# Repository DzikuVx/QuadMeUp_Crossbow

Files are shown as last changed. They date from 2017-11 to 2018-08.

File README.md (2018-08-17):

# QuadMeUp Crossbow

_QuadMeUp Crossbow_ is a DIY project that gives 5km (at least) of RC link for UAV (airplanes and drones) for a price below $40. I uses SX1278 (LoRa 868MHz/915MHz) compatible (like HopeRF RFM95W) radio modules connected to Arduino compatible boards. It can be regular Arduino connected via SPI to SX1278 or dedicated board like _Adafruit Feather 32u4 RFM LoRa_ or [LoRa32u4 II](http://bit.ly/2nJv9dd)

Future versions might be ported to [ESP32 LoRa32 modules](http://bit.ly/2BjG47d).

# Current state

Works:
* Getting data from OpenTX radio using SBUS protocol
* Transmitting 10 channels to RX modules
* Frequency hopping
* Getting basic telemetry from RX module
* Sending 10 channels using SBUS to flight controller
* Binding
* Allowing to use OLED on TX to get basic data

Needs implementation:
* TX module configuration
* RX configuration from TX module
* Sending telemetry from TX to OpenTX radio

# Dependencies

To compile, following libraries have to be installed:

* [U8g2](https://github.com/olikraus/u8g2) for OLED support in TX module
* [FlashStorage](https://github.com/cmaglie/FlashStorage) for EEPROM-Emulation if using a SAMD-Board (M0 etc.)

# Protocol

| Byte | Description | Notes |
| ---- | ---- | ---- |
| 1 | Frame type & used radio channel | bits 7-5 defines frame, bits 4-0 current radio channel |
| 2 - 33 | Payload | lenghth defined by frame type |
| payload length + 2 | CRC | using crc8_dvb_s2 method |

## CRC

CRC is computed using `crc8_dvb_s2` method. Initial CRC value for each frame CRC is equal to CRC of 4 bind bytes (unique for transmitter module). 

## Frame types

| Value  | Value hex | Description | Direction  | Payload length |
| ---- | ---- |---- | ---- | ---- |
| 0000 | 0x0 | RC channels data `RC_DATA` | TX -> RX | 9 |
| 0001 | 0x1 | Receiver health and basic telemetry `RX_HEALTH` | RX -> TX | 6 |
| 0010 | 0x2 | Request receiver configuration | TX -> RX | no used |
| 0011 | 0x3 | Receiver configuration | RX -> TX | no used |
| 0100 | 0x4 | Set receiver configuration | TX -> RX | no used |
| 0101 | 0x5 | PING frame, uses 9 byte payload | TX -> RX | 4 |
| 0110 | 0x6 | PONG frame, the same payload as PING | RX -> TX | 4 |
| 0111 | 0x7 | `BIND` frame, transmitted by TX only during binding | TX -> RX | 4 |

### `RC_DATA` frame format

Protocol allows to send 10 RC channels in total encoded as following

* channels 1 to 4 encoded using 10 bits each (5 bytes)
* channels 5 to 6 encoded using 8 bits each (2 bytes)
* channels 7 to 10 encoded using 4 bits per channel (2 bytes)

Total length of `RC_DATA` payload is 9 bytes

### `RX_HEALTH` frame format

| Byte  | Description |
| ----  | ---- |
| 1 | RX RSSI |
| 2 | RX SNR | 
| 3 | RX supply volatage, sent in 0,1V |
| 4 | RX analog input 1 sent in 0,1V |
| 5 | RX analog input 2 sent in 0,1V |
| 6 | Flags |

#### Flags

| Bit | Meaning |
| ----  | ---- |
| 00000001  | Device in Failsafe mode |

### `PING` and `PONG` frames

`PING` and `PONG` frames are to determine packet roundrip between **TX** and **RX** module.
**TX** sends `PING` frame with curent `micros`. If **RX** receives `PING` frame, it respons
its payload as `PONG` frame. 

### `BIND` frame format

| Byte  | Description |
| ----  | ---- |
| 1 | Bind key byte 0 |
| 2 | Bind key byte 1 |
| 3 | Bind key byte 2 |
| 4 | Bind key byte 3 |

# RSSI

1. Receiver RSSI for the last received packet is injected as channel 11
1. RSSI is scaled in **dB**, NOT **percent**
1. RSSI 0 in flight controller means 40dB RSSI in RF chip on last packet received  
1. RSSI 100 in flight controller means 140dB RSSI in RF chip on last packet received
1. Rule of thumb: to increase distance twice you need 6dB assuming nothing else will interfere
1. If at 100m RSSI is 40, at 200m should be around 34
1. I had successful flight with RSSI below `15`
1. With correct antennas, at 1km RSSI should be around `20` 

# OpenTX setup

OpenTX 2.2.1 or newer is required with enabled **External RF** SBUS.

* Mode: `SBUS`
* Channel Range: `1-16`
* Refresh rate: `12.0ms` or `14.0ms` `normal`

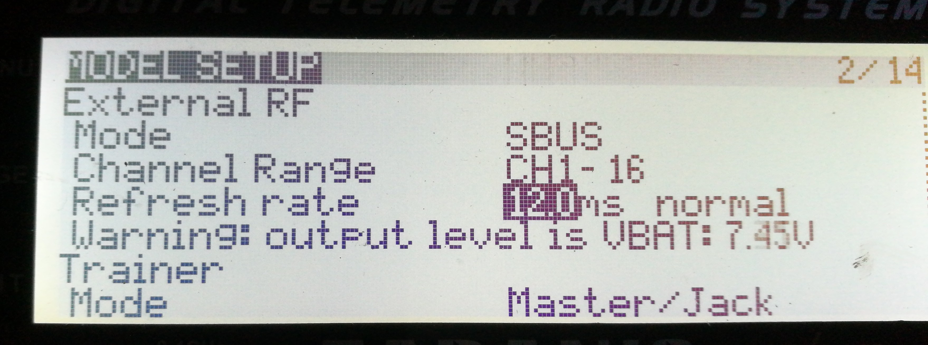
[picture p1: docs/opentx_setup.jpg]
OpenTX setup


Tested with:

* FrSky X9D Plus

# Flight controller setup

RX module outputs RC data using SBUS protocol. The trick is that DIY RX module does not have inverters, so SBUS signal is also not inverted (TTL standard), while standard SBUS protocol used inverted serial signal.

That mean the following:

* RX module TX line can be connected to any free UART RX pin
* On F3 or F7 boards flight controller has to be configured not to use inverted SBUS (refer to flight controller docs)
* On F4 flight controllers inverios has to be configured only when using dedicated SBUS serial port 

# Manual

## Binding

After flashing TX and RX, binding is required. 

1. Power up TX module
1. Navigate using button #1 to "Bind" option
1. Long press button #2 to enter _Bind Mode_
1. Power up RX
1. RX LED flashes quickly when in bind mode
1. After RX receives bind packet, LED goes to constanly _ON_ state
1. When RX LED is solid _ON_, leave bind mode by long pressing button #2 

# TX module connection diagram

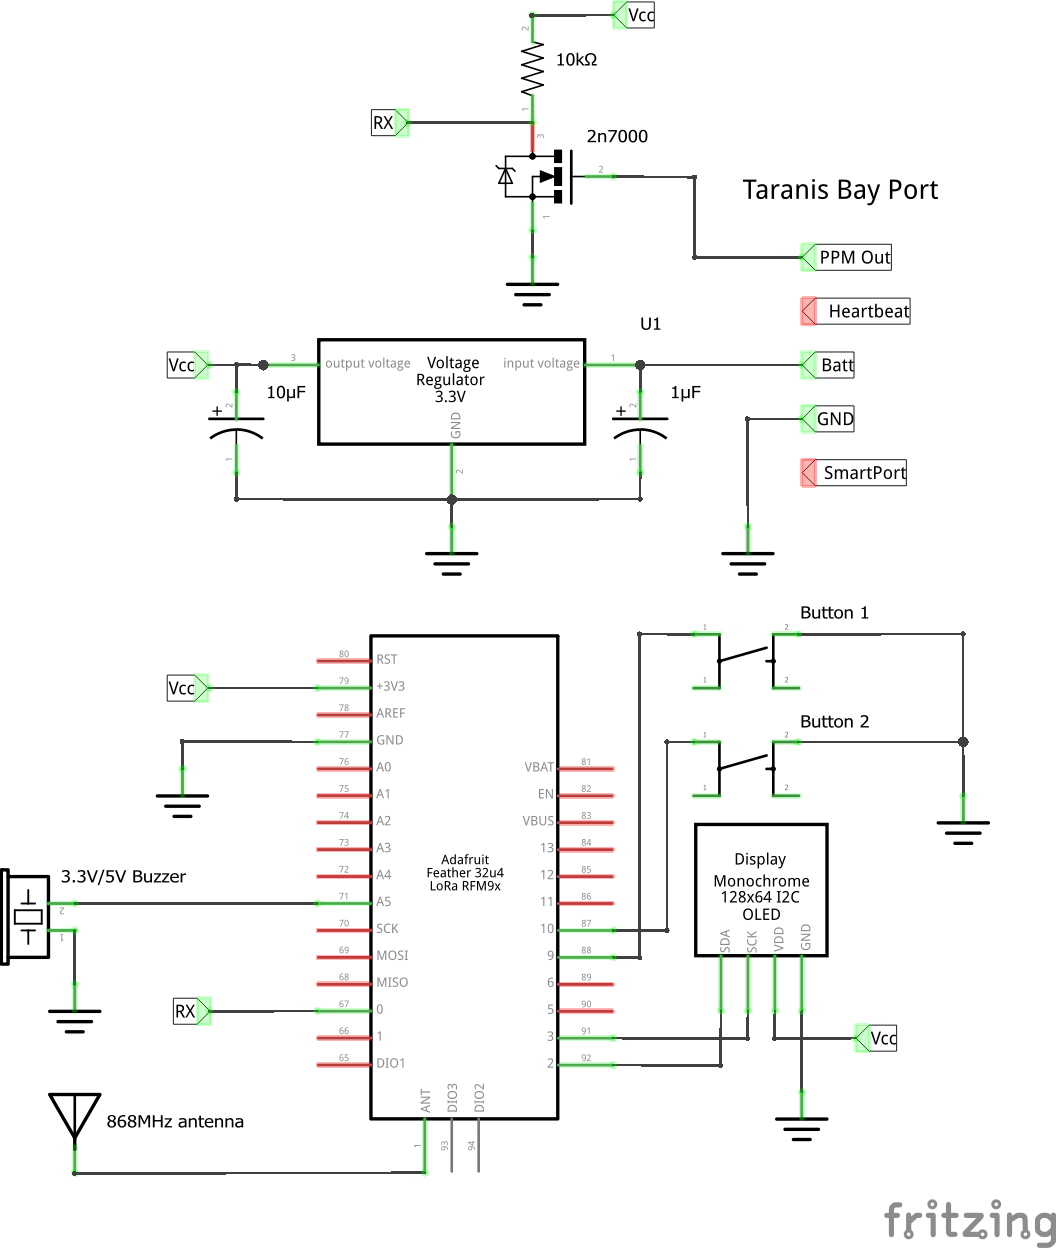
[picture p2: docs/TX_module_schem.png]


# RX module connection diagram

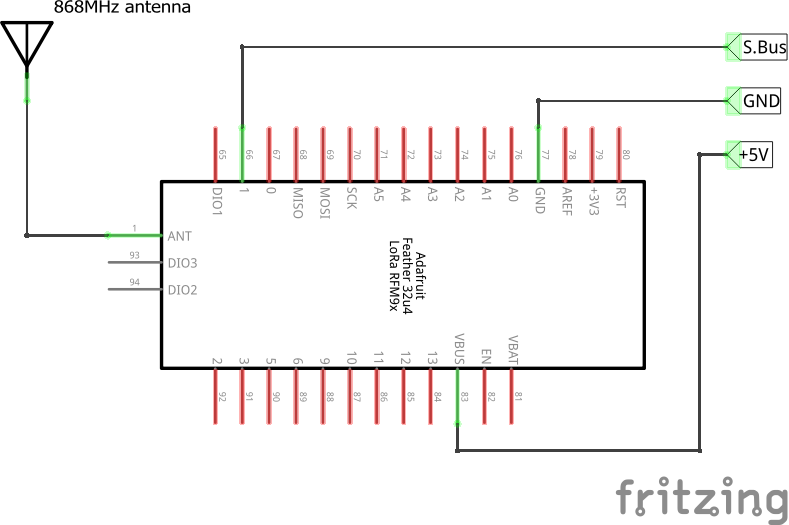
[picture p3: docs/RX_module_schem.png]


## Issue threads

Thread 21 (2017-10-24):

Add CRSF support on the TX module

DzikuVx, 2017-10-24:
PPM is crappy. Use CRSF protocol to get data from Taranis

DzikuVx, 2017-10-25:
Looks like LoRa32u4 (ATmega32u4 at 8MHz) is not fast enough to handle Serial at 420kbps. Serial data comes damaged

DieHertz, 2018-04-10:
200k another option

DieHertz, 2018-04-10:
So 8-bit is enough for everyone after all? :-D

DzikuVx, 2018-04-10:
I would not mind for longer serial buffer, but besides that, yes. "Micro" receiver will be a Arduino Pro Mini with piggybacked RFM95W on a double sided adhesive tape

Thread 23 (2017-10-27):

Send RX device state in RX_HEALTH frame to indicate RX in failsafe mode

DzikuVx, 2017-10-27:

Closed 2017-10-27.

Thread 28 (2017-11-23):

RF settings description

dontsovcmc, 2017-11-23:
Can you write something about RF settings? It's very important for reliable, delay and radius.. Thanks

    uint32_t frequency = 867000000;
    uint32_t loraBandwidth = 250000;
    uint8_t loraSpreadingFactor = 7;
    uint8_t loraCodingRate = 6;

Why you don't change TxPower?

    LoRa.setTxPower(17); //2-17

Thanks!

DzikuVx, 2017-11-23:
Those value seems to be working pretty well. It's a compromise between range and delay. At 25mW (14dBm) I was able to test at 3km range on the ground with few dB of budget link still to spare. At few meters above the ground.

For the second question, default is 50mW (17dBm) at it is the strongest allowed output power for SX1276 without duty cycle limitation

DzikuVx, 2017-11-23:
Let's say solved in 8ffaccbd5fdc0b2bb4a06b334f99e6f50e6e6bbb

Closed 2017-11-23.

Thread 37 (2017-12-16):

Improve TX module indication

DzikuVx, 2017-12-16:
onboard led should be blinking if radio is working normally

DzikuVx, 2018-04-27:
* blink fast when frames are received from radio
* blink slowly when TX is getting RX telemetry
* be constantly on when no input and no telemetry

Closed 2018-04-28.

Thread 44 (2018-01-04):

Frame length should be hardcoded

DzikuVx, 2018-01-04:
Frame length should be hardcoded to frame type.
Do not send frame length, get it from frame type.
Available 4 bits in header can be used to send current channel

DzikuVx, 2018-04-10:
done in #48

Closed 2018-04-10.

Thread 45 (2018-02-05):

Which libraries do you use?

unitware, 2018-02-05:
I'm trying to locate correct sources and versions of all libraries but I'm not sure I got it correct. It would be great if you could help me out, maybe update the readme?

My PPMReader (https://github.com/Nikkilae/PPM-reader) does not match the function prototype
"
crossbow:38: error: no matching function for call to 'PPMReader::PPMReader(int, int, bool)'
 PPMReader ppmReader(PPM_INPUT_PIN, PPM_INPUT_INTERRUPT, true);
"

Then I need to fix the InterruptHandler to support the M0 chip but thats another story :)

unitware, 2018-02-05:
ok, I was using the wrong lib, Just found your https://github.com/DzikuVx/PPMReader which I assume is the correct one. But then I realized that you are using sbus from your transceiver..

I have also found:
https://github.com/adafruit/Adafruit_SSD1306
https://github.com/adafruit/Adafruit-GFX-Library

which seems to work.

unitware, 2018-02-05:
Have you used the PPMReader at the same time as the lora library? I am having trouble getting communications to run when I am instansiating the ppmReader, interuppt conflict?

DzikuVx, 2018-02-06:
PPM reader is not longer used in current code. The only external lib would be Adafruit_SSD1306. Everything else is part of the project itself

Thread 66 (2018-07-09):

Issues on M0

kadrim, 2018-07-09:
Hi there,

i tried your code on adafruit m0 and it needs adjustmends, because the M0 does not have an EEPROM.

In platform_node.h:

`#ifdef ARDUINO_AVR_FEATHER32U4
#include <EEPROM.h>
#endif`

In platform_node.cpp:
`
void PlatformNode::seed(void) {
    uint8_t val;
#ifdef ARDUINO_AVR_FEATHER32U4
    val = EEPROM.read(EEPROM_ADDRESS_BIND_KEY_SEEDED);

    if (val != 0xf1) {
        EEPROM.write(EEPROM_ADDRESS_BIND_0, random(1, 255)); //Yes, from 1 to 254
        EEPROM.write(EEPROM_ADDRESS_BIND_1, random(1, 255)); //Yes, from 1 to 254
        EEPROM.write(EEPROM_ADDRESS_BIND_2, random(1, 255)); //Yes, from 1 to 254
        EEPROM.write(EEPROM_ADDRESS_BIND_3, random(1, 255)); //Yes, from 1 to 254
        EEPROM.write(EEPROM_ADDRESS_BIND_KEY_SEEDED, 0xf1);
    }
#endif
}

void PlatformNode::loadBindKey(uint8_t key[]) {
#ifdef ARDUINO_AVR_FEATHER32U4
    key[0] = EEPROM.read(EEPROM_ADDRESS_BIND_0);
    key[1] = EEPROM.read(EEPROM_ADDRESS_BIND_1);
    key[2] = EEPROM.read(EEPROM_ADDRESS_BIND_2);
    key[3] = EEPROM.read(EEPROM_ADDRESS_BIND_3);
#endif
}

void PlatformNode::saveBindKey(uint8_t key[]) {
#ifdef ARDUINO_AVR_FEATHER32U4
    EEPROM.write(EEPROM_ADDRESS_BIND_0, key[0]);
    EEPROM.write(EEPROM_ADDRESS_BIND_1, key[1]);
    EEPROM.write(EEPROM_ADDRESS_BIND_2, key[2]);
    EEPROM.write(EEPROM_ADDRESS_BIND_3, key[3]);
    EEPROM.write(EEPROM_ADDRESS_BIND_KEY_SEEDED, 0xf1);
#endif
}
`

Best regards,
David

DzikuVx, 2018-07-10:
Hi,

Unfortunately, EEPROM or some way to store configuration is currently required. I do not have M0 so if noone will find a solution on M0, I will have to drop support for it

kadrim, 2018-07-10:
I have some M0 lying around - i will fiddle around with them and try to provide a solution, i.e. using Flash-Memory

DzikuVx, 2018-07-10:
Yes, that would be the best

kadrim, 2018-07-10:
I created a pull request for this issue: https://github.com/DzikuVx/QuadMeUp_Crossbow/pull/67

Best regards
David

kadrim, 2018-07-10:
Resolved

Closed 2018-07-10.

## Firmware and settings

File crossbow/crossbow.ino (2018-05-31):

/*
This Source Code Form is subject to the terms of the Mozilla Public
License, v. 2.0. If a copy of the MPL was not distributed with this file,
You can obtain one at http://mozilla.org/MPL/2.0/.

Copyright (c) 20xx, MPL Contributor1 contrib1@example.net
*/

#include "config.h"

#include "lora.h"
#include "radio_node.h"
#include "variables.h"
#include "main_variables.h"
#include "qsp.h"
#include "sbus.h"
#include "platform_node.h"

#ifdef ARDUINO_AVR_FEATHER32U4
    #define LORA_SS_PIN     8
    #define LORA_RST_PIN    4
    #define LORA_DI0_PIN    7

    #define BUTTON_0_PIN    9
    #define BUTTON_1_PIN    10
#elif defined(ARDUINO_SAMD_FEATHER_M0)
    #define LORA_SS_PIN     8
    #define LORA_RST_PIN    4
    #define LORA_DI0_PIN    3

    #define BUTTON_0_PIN    9 //Please verify
    #define BUTTON_1_PIN    10 //Please verify
#else
    #error please select hardware
#endif

RadioNode radioNode;
PlatformNode platformNode;

/*
 * Main defines for device working in TX mode
 */
#ifdef DEVICE_MODE_TX

#ifdef FEATURE_TX_INPUT_PPM
  #include "ppm_reader.h"
  PPM_Reader txInput(PPM_INPUT_PIN, true);

#elif defined(FEATURE_TX_INPUT_SBUS)
  #include "sbus.h"
  SbusInput txInput(Serial1);

#else
  #error please select tx input source
#endif

#include "txbuzzer.h"

BuzzerState_t buzzer;

#ifdef FEATURE_TX_OLED
#include "tx_oled.h"
TxOled oled;
#endif

#include "tactile.h"

Tactile button0(BUTTON_0_PIN);
Tactile button1(BUTTON_1_PIN);

#endif

/*
 * Main defines for device working in RX mode
 */
#ifdef DEVICE_MODE_RX
    uint32_t sbusTime = 0;
    uint8_t sbusPacket[SBUS_PACKET_LENGTH] = {0};
    uint32_t lastRxStateTaskTime = 0;
#endif

/*
 * Start of QSP protocol implementation
 */
QspConfiguration_t qsp = {};
RxDeviceState_t rxDeviceState = {};
TxDeviceState_t txDeviceState = {};

void onQspSuccess(QspConfiguration_t *qsp, TxDeviceState_t *txDeviceState, RxDeviceState_t *rxDeviceState, uint8_t receivedChannel) {
    //If recide received a valid frame, that means it can start to talk
    radioNode.lastReceivedChannel = receivedChannel;
    
    //RX can start transmitting only when an least one frame has been receiveds
    radioNode.canTransmit = true;

    radioNode.readRssi();
    radioNode.readSnr();

    /*
     * RX module hops to next channel after frame has been received
     */
#ifdef DEVICE_MODE_RX
    if (!platformNode.isBindMode) {
        //We do not hop frequency in bind mode!
        radioNode.hopFrequency(true, radioNode.lastReceivedChannel, millis());
        radioNode.failedDwellsCount = 0; // We received a frame, so we can just reset this counter
        LoRa.receive(); //Put radio back into receive mode
    }
#endif

    //Store the last timestamp when frame was received
    if (qsp->frameId < QSP_FRAME_COUNT) {
        qsp->lastFrameReceivedAt[qsp->frameId] = millis();
    }
    qsp->anyFrameRecivedAt = millis();
    switch (qsp->frameId) {
        case QSP_FRAME_RC_DATA:
            qspDecodeRcDataFrame(qsp, rxDeviceState);
            break;

        case QSP_FRAME_RX_HEALTH:
            decodeRxHealthPayload(qsp, rxDeviceState);
            break;

        case QSP_FRAME_PING:
            qsp->forcePongFrame = true;
            break;

        case QSP_FRAME_BIND:
#ifdef DEVICE_MODE_RX
            if (platformNode.isBindMode) {
                platformNode.bindKey[0] = qsp->payload[0];
                platformNode.bindKey[1] = qsp->payload[1];
                platformNode.bindKey[2] = qsp->payload[2];
                platformNode.bindKey[3] = qsp->payload[3];

                platformNode.saveBindKey(platformNode.bindKey);
                platformNode.leaveBindMode();
            }
#endif
            break;

        case QSP_FRAME_PONG:
            txDeviceState->roundtrip = qsp->payload[0];
            txDeviceState->roundtrip += (uint32_t) qsp->payload[1] << 8;
            txDeviceState->roundtrip += (uint32_t) qsp->payload[2] << 16;
            txDeviceState->roundtrip += (uint32_t) qsp->payload[3] << 24;

            txDeviceState->roundtrip = (micros() - txDeviceState->roundtrip) / 1000;
            break;

        default:
            //Unknown frame
            //TODO do something in this case
            break;
    }

    qsp->transmitWindowOpen = true;
}

void onQspFailure(QspConfiguration_t *qsp, TxDeviceState_t *txDeviceState, RxDeviceState_t *rxDeviceState) {

}

//I do not get function pointers to object methods, no way...
int getRcChannel_wrapper(uint8_t channel) {
    return platformNode.getRcChannel(channel);
}

//Same here, wrapper just works
void setRcChannel_wrapper(uint8_t channel, int value, int offset) {
    platformNode.setRcChannel(channel, value, offset);
}

void setup(void)
{
#ifdef DEBUG_SERIAL
    Serial.begin(115200);
#endif

    qsp.onSuccessCallback = onQspSuccess;
    qsp.onFailureCallback = onQspFailure;
    qsp.rcChannelGetCallback = getRcChannel_wrapper;
    qsp.setRcChannelCallback = setRcChannel_wrapper;

#ifdef DEVICE_MODE_RX
    platformNode.platformState = DEVICE_STATE_FAILSAFE;
#else
    platformNode.platformState = DEVICE_STATE_OK;

    txInput.setRcChannelCallback = setRcChannel_wrapper;

#endif

    radioNode.init(LORA_SS_PIN, LORA_RST_PIN, LORA_DI0_PIN, onReceive);

#ifdef DEVICE_MODE_RX

    pinMode(RX_ADC_PIN_1, INPUT);
    pinMode(RX_ADC_PIN_2, INPUT);
    pinMode(RX_ADC_PIN_3, INPUT);

    /*
     * Prepare Serial1 for S.Bus processing
     */
    Serial1.begin(100000, SERIAL_8E2);

    platformNode.enterBindMode();
    LoRa.receive(); //TODO this probably should be moved somewhere....
#endif

#ifdef DEVICE_MODE_TX

    randomSeed(analogRead(A4));
    platformNode.seed();

#ifdef FEATURE_TX_OLED
    oled.init();
    oled.page(TX_PAGE_INIT);
#endif

    /*
     * TX should start talking imediately after power up
     */
    radioNode.canTransmit = true;

    pinMode(TX_BUZZER_PIN, OUTPUT);

    //Play single tune to indicate power up
    buzzerSingleMode(BUZZER_MODE_CHIRP, &buzzer);

    /*
     * Prepare Serial1 for S.Bus processing
     */
    txInput.start();

    /*
     * Buttons on TX module
     */
    button0.start();
    button1.start();

    platformNode.loadBindKey(platformNode.bindKey);

#endif

    pinMode(LED_BUILTIN, OUTPUT);
}

uint8_t currentSequenceIndex = 0;
#define TRANSMIT_SEQUENCE_COUNT 16

#ifdef DEVICE_MODE_RX

void updateRxDeviceState(RxDeviceState_t *rxDeviceState) {
    rxDeviceState->rxVoltage = map(analogRead(RX_ADC_PIN_1), 0, 1024, 0, 255);
    rxDeviceState->a1Voltage = map(analogRead(RX_ADC_PIN_2), 0, 1024, 0, 255);
    rxDeviceState->a2Voltage = map(analogRead(RX_ADC_PIN_3), 0, 1024, 0, 255);
}

int8_t getFrameToTransmit(QspConfiguration_t *qsp) {

    if (qsp->forcePongFrame) {
        qsp->forcePongFrame = false;
        return QSP_FRAME_PONG;
    }

    int8_t retVal = rxSendSequence[currentSequenceIndex];

    currentSequenceIndex++;
    if (currentSequenceIndex >= TRANSMIT_SEQUENCE_COUNT) {
        currentSequenceIndex = 0;
    }

    return retVal;
}

#endif

#ifdef DEVICE_MODE_TX
int8_t getFrameToTransmit(QspConfiguration_t *qsp) {

    if (platformNode.isBindMode) {
        return QSP_FRAME_BIND;
    }

    int8_t retVal = txSendSequence[currentSequenceIndex];

    currentSequenceIndex++;
    if (currentSequenceIndex >= TRANSMIT_SEQUENCE_COUNT) {
        currentSequenceIndex = 0;
    }

    return retVal;
}
#endif

/*
 *
 * Main loop starts here!
 *
 */
void loop(void)
{

    static uint32_t nextKey = millis();

    uint32_t currentMillis = millis();

#ifdef DEVICE_MODE_RX

    //Make sure to leave bind mode when binding is done
    if (platformNode.isBindMode && millis() > platformNode.bindModeExitMillis) {
        platformNode.leaveBindMode();
    }

    /*
     * This routine handles resync of TX/RX while hoppping frequencies
     * When not in bind mode. Bind mode is single frequency operation
     */
    if (!platformNode.isBindMode) {
        radioNode.handleChannelDwell();
    }

    /*
     * Detect the moment when radio module stopped transmittig and put it
     * back in to receive state
     */
    radioNode.handleTxDoneState(false);
#else 

    //Process buttons
    button0.loop();
    button1.loop();

#ifdef FEATURE_TX_OLED
    oled.loop();
#endif

    txInput.recoverStuckFrames();

    /*
     * If we are not receiving SBUS frames from radio, try to restart serial
     */
    static uint32_t serialRestartMillis = 0;

    /*
     * Final guard for SBUS input. If there is no input, try to restart serial port
     */
    if (!txInput.isReceiving() && serialRestartMillis + 100 < currentMillis) {
        txInput.restart();
        serialRestartMillis = currentMillis;
    }

    radioNode.handleTxDoneState(!platformNode.isBindMode);
#endif

    radioNode.readAndDecode(
        &qsp,
        &rxDeviceState,
        &txDeviceState,
        platformNode.bindKey
    );

    bool transmitPayload = false;

    /*
     * Watchdog for frame decoding stuck somewhere in the middle of a process
     */
    if (
        qsp.protocolState != QSP_STATE_IDLE &&
        qsp.frameDecodingStartedAt + QSP_MAX_FRAME_DECODE_TIME < currentMillis
    ) {
        qsp.protocolState = QSP_STATE_IDLE;
    }

#ifdef DEVICE_MODE_TX

    txInput.loop();

    if (
        radioNode.radioState == RADIO_STATE_RX &&
        qsp.protocolState == QSP_STATE_IDLE &&
        qsp.lastTxSlotTimestamp + TX_TRANSMIT_SLOT_RATE < currentMillis
    ) {
        
        int8_t frameToSend = getFrameToTransmit(&qsp);

    #ifndef FORCE_TX_WITHOUT_INPUT
        /*
         * If module is not receiving data from radio, do not send RC DATA
         * This is the only way to trigger failsafe in that case
         */
        if (frameToSend == QSP_FRAME_RC_DATA && !txInput.isReceiving()) {
            frameToSend = -1;
        }
    #endif

        if (frameToSend > -1) {

            qsp.frameToSend = frameToSend;
            qspClearPayload(&qsp);

            switch (qsp.frameToSend) {
                case QSP_FRAME_PING:
                    encodePingPayload(&qsp, micros());
                    break;

                case QSP_FRAME_RC_DATA:
                    encodeRcDataPayload(&qsp, PLATFORM_CHANNEL_COUNT);
                    break;

                case QSP_FRAME_BIND:

                    /*
                     * Key to be transmitted is stored in EEPROM
                     * During binding different key is used
                     */ 
                    uint8_t key[4];
                    platformNode.loadBindKey(key);

                    encodeBindPayload(&qsp, key);
                    break;
            }

            transmitPayload = true;
        }

        qsp.lastTxSlotTimestamp = currentMillis;
    }

#endif

#ifdef DEVICE_MODE_RX
    /*
     * This routine updates RX device state and updates one of radio channels with RSSI value
     */
    if (lastRxStateTaskTime + RX_TASK_HEALTH < currentMillis) {
        lastRxStateTaskTime = currentMillis;
        updateRxDeviceState(&rxDeviceState);

        uint8_t output = constrain(radioNode.rssi - 40, 0, 100);

        rxDeviceState.indicatedRssi = (output * 10) + 1000;
    }

    /*
     * Main routine to answer to TX module
     */
    if (qsp.transmitWindowOpen && qsp.protocolState == QSP_STATE_IDLE) {
        qsp.transmitWindowOpen = false;

        int8_t frameToSend = getFrameToTransmit(&qsp);
        if (frameToSend > -1) {
            qsp.frameToSend = frameToSend;

            if (frameToSend != QSP_FRAME_PONG) {
                qspClearPayload(&qsp);
            }
            switch (qsp.frameToSend) {
                case QSP_FRAME_PONG:
                    /*
                     * Pong frame just responses with received payload
                     */
                    break;

                case QSP_FRAME_RX_HEALTH:
                    encodeRxHealthPayload(
                        &qsp, 
                        &rxDeviceState, 
                        radioNode.rssi, 
                        radioNode.snr, 
                        (platformNode.platformState == DEVICE_STATE_FAILSAFE)
                    );
                    break;
            }

            transmitPayload = true;
        }

    }

    if (currentMillis > sbusTime) {
        platformNode.setRcChannel(RSSI_CHANNEL - 1, rxDeviceState.indicatedRssi, 0);

        sbusPreparePacket(sbusPacket, false, (platformNode.platformState == DEVICE_STATE_FAILSAFE), getRcChannel_wrapper);
        Serial1.write(sbusPacket, SBUS_PACKET_LENGTH);
        sbusTime = currentMillis + SBUS_UPDATE_RATE;
    }

    if (qsp.lastFrameReceivedAt[QSP_FRAME_RC_DATA] + RX_FAILSAFE_DELAY < currentMillis) {
        platformNode.platformState = DEVICE_STATE_FAILSAFE;
        rxDeviceState.indicatedRssi = 0;
        radioNode.rssi = 0;
    } else {
        platformNode.platformState = DEVICE_STATE_OK;
    }

#endif

    if (transmitPayload)
    {
        radioNode.handleTx(&qsp, platformNode.bindKey);
    }

#ifdef DEVICE_MODE_TX

    buzzerProcess(TX_BUZZER_PIN, currentMillis, &buzzer);

    // This routing enables when TX starts to receive signal from RX for a first time or after
    // failsafe
    if (txDeviceState.isReceiving == false && qsp.anyFrameRecivedAt != 0) {
        //TX module started to receive data
        buzzerSingleMode(BUZZER_MODE_DOUBLE_CHIRP, &buzzer);
        txDeviceState.isReceiving = true;
        platformNode.platformState = DEVICE_STATE_OK;
    }

    //Here we detect failsafe state on TX module
    if (
        txDeviceState.isReceiving &&
        qsp.anyFrameRecivedAt + TX_FAILSAFE_DELAY < currentMillis
    ) {
        txDeviceState.isReceiving = false;
        rxDeviceState.a1Voltage = 0;
        rxDeviceState.a2Voltage = 0;
        rxDeviceState.rxVoltage = 0;
        rxDeviceState.rssi = 0;
        rxDeviceState.snr = 0;
        rxDeviceState.flags = 0;
        txDeviceState.roundtrip = 0;
        platformNode.platformState = DEVICE_STATE_FAILSAFE;
        qsp.anyFrameRecivedAt = 0;
    }

    //FIXME rxDeviceState should be resetted also in RC_HEALT frame is not received in a long period

    //Handle audible alarms
    if (platformNode.platformState == DEVICE_STATE_FAILSAFE) {
        //Failsafe detected by TX
        buzzerContinousMode(BUZZER_MODE_SLOW_BEEP, &buzzer);
    } else if (txDeviceState.isReceiving && (rxDeviceState.flags & 0x1) == 1) {
        //Failsafe reported by RX module
        buzzerContinousMode(BUZZER_MODE_SLOW_BEEP, &buzzer);
    } else if (txDeviceState.isReceiving && radioNode.rssi < 45) {
        buzzerContinousMode(BUZZER_MODE_DOUBLE_CHIRP, &buzzer); // RSSI below 45dB // Critical state
    } else if (txDeviceState.isReceiving && radioNode.rssi < 55) {
        buzzerContinousMode(BUZZER_MODE_CHIRP, &buzzer); // RSSI below 55dB // Warning state
    } else {
        buzzerContinousMode(BUZZER_MODE_OFF, &buzzer);
    }

#endif

    /*
     * Handle LED updates
     */
    if (platformNode.nextLedUpdate < currentMillis) {
#ifdef DEVICE_MODE_TX
        if (txDeviceState.isReceiving) {
            digitalWrite(LED_BUILTIN, !digitalRead(LED_BUILTIN));
            platformNode.nextLedUpdate = currentMillis + 300;
        } else if (txInput.isReceiving()) {
            digitalWrite(LED_BUILTIN, !digitalRead(LED_BUILTIN));
            platformNode.nextLedUpdate = currentMillis + 100;
        } else {
            digitalWrite(LED_BUILTIN, HIGH);
            platformNode.nextLedUpdate = currentMillis + 200;
        }
#else

        if (platformNode.isBindMode) {
            platformNode.nextLedUpdate = currentMillis + 50;
            digitalWrite(LED_BUILTIN, !digitalRead(LED_BUILTIN));
        } else {
            platformNode.nextLedUpdate = currentMillis + 200;

            if (platformNode.platformState == DEVICE_STATE_FAILSAFE) {
                digitalWrite(LED_BUILTIN, HIGH);
            } else {
                digitalWrite(LED_BUILTIN, !digitalRead(LED_BUILTIN));
            }
        }
#endif
    }

}

void onReceive(int packetSize)
{
    /*
     * We can start reading only when radio is not reading.
     * If not reading, then we might start
     */
    if (radioNode.bytesToRead == NO_DATA_TO_READ) {
        if (packetSize >= MIN_PACKET_SIZE && packetSize <= MAX_PACKET_SIZE) {
            //We have a packet candidate that might contain a valid QSP packet
            radioNode.bytesToRead = packetSize;
        } else {
            /*
            That packet was not very interesting, just flush it, we have no use
            */
            LoRa.sleep();
            LoRa.receive();
            radioNode.radioState = RADIO_STATE_RX;
        }
    }
}

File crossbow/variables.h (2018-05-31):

#include "Arduino.h"

#pragma once

#ifndef VARIABLES_H
#define VARIABLES_H

#define RADIO_STATE_TX 1
#define RADIO_STATE_RX 2

#define TX_TRANSMIT_SLOT_RATE 67 //ms
#define RX_CHANNEL_DWELL_TIME (TX_TRANSMIT_SLOT_RATE + 10) //Dwell on a channel slightly longer 
#define RX_FAILSAFE_DELAY (TX_TRANSMIT_SLOT_RATE * 8)
#define TX_FAILSAFE_DELAY (RX_FAILSAFE_DELAY * 4)

#define SBUS_UPDATE_RATE 15 //ms
#define SBUS_PACKET_LENGTH 25

#define RC_CHANNEL_MIN 990
#define RC_CHANNEL_MAX 2010

#define RX_TASK_HEALTH 200 //5Hz should be enough
#define RSSI_CHANNEL 11

#define QSP_PAYLOAD_LENGTH 32

#define QSP_MAX_FRAME_DECODE_TIME 10 //max time that frame can be decoded in ms

#define QSP_FRAME_RC_DATA 0x0
#define QSP_FRAME_RX_HEALTH 0x1
#define QSP_FRAME_GET_RX_CONFIG 0x2
#define QSP_FRAME_RX_CONFIG 0x3
#define QSP_FRAME_SET_RX_CONFIG 0x4
#define QSP_FRAME_PING 0x5
#define QSP_FRAME_PONG 0x6
#define QSP_FRAME_BIND 0x7
#define QSP_FRAME_COUNT 0x8

static const uint8_t qspFrameLengths[QSP_FRAME_COUNT] = {
    9, //QSP_FRAME_RC_DATA
    6, //QSP_FRAME_RX_HEALTH
    0, //QSP_FRAME_GET_RX_CONFIG -> Not used
    0, //QSP_FRAME_RX_CONFIG -> Not used
    0, //QSP_FRAME_SET_RX_CONFIG -> Not used
    4, //QSP_FRAME_PING
    4, //QSP_FRAME_PONG
    4  //QSP_FRAME_BIND
};

#define RX_ADC_PIN_1 A0
#define RX_ADC_PIN_2 A1
#define RX_ADC_PIN_3 A2

enum dataStates {
    QSP_STATE_IDLE,
    QSP_STATE_FRAME_TYPE_RECEIVED,
    QSP_STATE_PAYLOAD_RECEIVED,
    QSP_STATE_CRC_RECEIVED
};

#define PPM_INPUT_PIN       0 // Has to be one of Interrupt pins

#define TX_BUZZER_PIN A5

#define PPM_FRAME_LENGTH 30500  //set the PPM frame length in microseconds (1ms = 1000µs)
#define PPM_PULSE_LENGTH 300  //set the pulse length
#define PPM_OUTPUT_MULTIPLIER 1 //1 for 8MHz RX, 2 for 16MHz RX
#define PPM_SIGNAL_POSITIVE_STATE 1  //set polarity of the pulses: 1 is positive, 0 is negative
#define PPM_OUTPUT_PIN 10  //set PPM signal output pin on the arduino

#define MIN_PACKET_SIZE 3 //Min theorethical size of valid packet 
#define MAX_PACKET_SIZE 20 //Max theorethical size of valid packet

#define NO_DATA_TO_READ -1

struct TxDeviceState_t {
    uint8_t flags = 0;
    uint32_t roundtrip = 0;
    bool isReceiving = false; //Indicates that TX module is receiving frames from RX module
};

struct RxDeviceState_t {
    uint8_t rssi = 0;
    uint8_t snr = 0;
    uint8_t rxVoltage = 0;
    uint8_t a1Voltage = 0;
    uint8_t a2Voltage = 0;
    uint8_t flags = 0;
    int16_t indicatedRssi = 0;
};

struct QspConfiguration_t {
    uint8_t protocolState = QSP_STATE_IDLE;
    uint8_t crc = 0;
    uint8_t payload[QSP_PAYLOAD_LENGTH] = {0};
    uint8_t payloadLength = 0;
    uint8_t frameToSend = 0;
    uint8_t frameId = 0;
    uint32_t lastFrameReceivedAt[QSP_FRAME_COUNT] = {0};
    uint32_t anyFrameRecivedAt = 0;
    void (* onSuccessCallback)(QspConfiguration_t*, TxDeviceState_t*, RxDeviceState_t*, uint8_t receivedChannel);
    void (* onFailureCallback)(QspConfiguration_t*, TxDeviceState_t*, RxDeviceState_t*);    
    int (* rcChannelGetCallback)(uint8_t);
    void (* setRcChannelCallback)(uint8_t channel, int value, int offset);
    bool forcePongFrame = false;
    uint32_t frameDecodingStartedAt = 0;
    uint32_t lastTxSlotTimestamp = 0;
    bool transmitWindowOpen = false;
};

#endif

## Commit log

2017-09-23 RC_DATA protocol frame updated
2017-09-24 RC_DATA frame encoded
2017-09-27 encoding of RC_DATA frame
2017-09-27 Correct way of encoding RC_DATA frame
    [common.h, crossbow.ino]
2017-09-30 Support for SPI connected SX1278
2017-10-11 RX failsafe with pulling PPM output LOW
    [crossbow.ino, variables.h]
2017-10-12 Store last time frame was received
2017-10-12 Rx_health frame encoding, no data is yet acquired from Rx hardware
2017-10-20 Fixed SPI mode with LoRa32u4 II
    [crossbow.ino, variables.h]
2017-10-25 LED blink on RX when receiving, Constant on FAILSAFE
    [crossbow.ino]
2017-10-26 Sloted approach on TX side
2017-10-26 Slots for transmitting on RX side close #8
2017-10-27 TX module is no longer using interrupts to read from LoRa. This fixes jumpy PPM readouts
    [crossbow.ino, variables.h]
2017-10-27 Fixed race condition that casued concurrent SPI operation and hunged the RX module
    [crossbow.ino]
2017-10-28 Basic buzzer framework
2017-10-28 Reduced number of SPI operations when reading RF packets
2017-10-29 Buzzer Single and Continous modes
    [crossbow.ino, txbuzzer.cpp]
2017-10-30 Fixed casting bug on RX side that was causing failsafe to engage without specific reason
    [crossbow.ino]
2017-10-30 Several small fixes for potential race conditions
    [crossbow.ino]
2017-11-04 RX module schema
    [RX module.fzz]
2017-11-07 diagram for RX module
    [RX_module.fzz]
2017-11-09 Fixed bug thata was failing to process frames without preamble
    [crossbow.ino, variables.h]
2017-11-15 Reworked radio handling to early reject false packets
    [crossbow.ino, variables.h]
2017-11-18 RSSI buzzer alarms adjusted
    [crossbow.ino]
2017-11-19 TX module diagram
    [TX_module.fzz]
2017-11-23 TX power moved to configuration
2017-12-01 Arduino LoRa library is now part of package
2017-12-14 Packet reading is now down in single SPI transaction
2017-12-15 TX happening in single SPI transaction
2017-12-16 LoRa non-blocking endPacket from https://github.com/sandeepmistry/arduino-LoRa/pull/62
2018-01-03 I2C speed bumped to 400kHz
2018-01-03 Improved failsafe state detection when TX module is not receiving input
    [crossbow.ino, sbus.cpp]
2018-01-03 Fixed serial on TX
    [crossbow.ino]
2018-04-10 frame payload lengths is now const. depending on frame type
2018-04-10 ensure pin DIO0 is set to input
2018-04-10 new features ported from Arduino-LoRa library
2018-04-19 improed processing of sbus frames
2018-04-19 Fixed current channel indication and next channel computation
    [crossbow.ino, variables.h]
2018-04-26 hardcoded 4 byte binding key
    [crossbow.ino, variables.h]
2018-04-26 Bind key used to init frame CRC
2018-04-27 TX module LED indication
2018-04-28 Improved sbus handling with a possibility to abandon stuck SBUS frames
    [crossbow.ino, sbus.cpp]
2018-05-14 Very ugly button handling
2018-05-14 Basic buttons framework fixes
    [crossbow.ino]
2018-05-15 Basic OLED framework with start and info pages
2018-05-15 do not store pointers, this just do not work
    [crossbow.ino]
2018-05-23 Some work, stuck by dependencies
    [crossbow.ino, platform_node.h, radio_node.h]
2018-05-23 Outgoing bind frame
2018-05-28 fixed binding key in bind mode
    [crossbow.ino, platform_node.h]
2018-05-31 Correctly working binding mode
    [crossbow.ino, platform_node.h]
2018-05-31 Docs update
    [TX_module.fzz]
2018-07-10 added dependency for FlashStorage if using a SAMD-Board
